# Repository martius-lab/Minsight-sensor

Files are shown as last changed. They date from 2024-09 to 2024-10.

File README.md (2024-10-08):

# Minsight: A Fingertip-Sized Vision-Based Tactile Sensor for Robotic Manipulation

This project provides manufacturing details and files for [Minsight](https://onlinelibrary.wiley.com/doi/full/10.1002/aisy.202300042). It is a soft fingertip-sized tactile sensor that can sense 3D forces over its whole sensing surface.

The corresponding paper is titled "[Minsight: A Fingertip-Sized Vision-Based Tactile Sensor for Robotic Manipulation](https://onlinelibrary.wiley.com/doi/full/10.1002/aisy.202300042)", published in *Advanced Intelligent Systems*, 2023. 

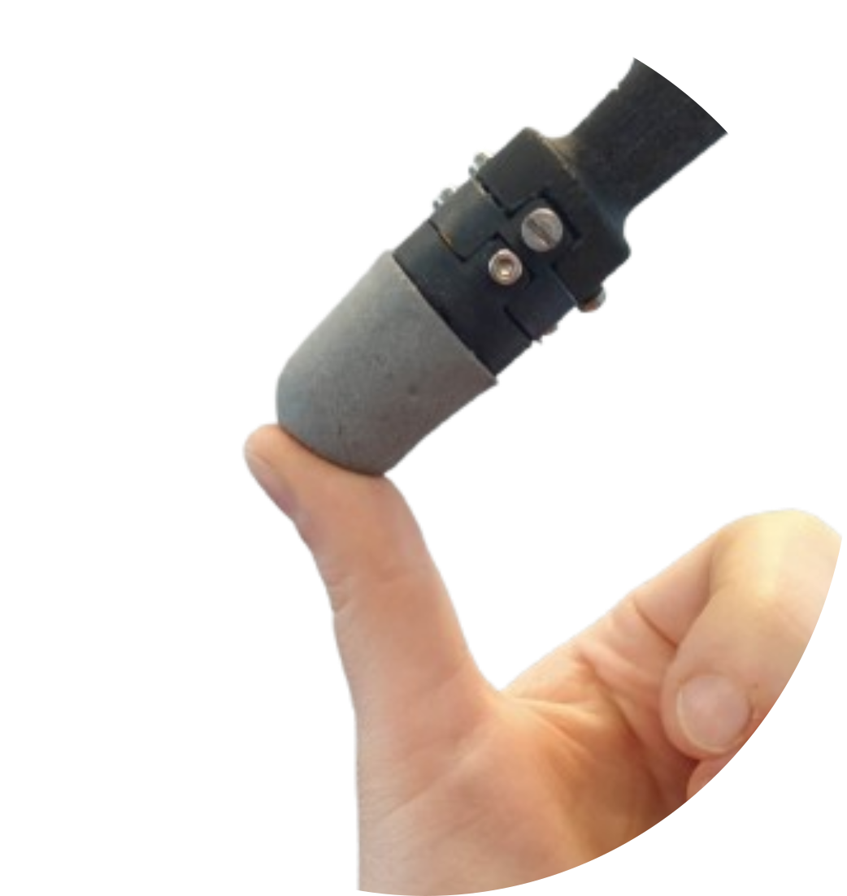
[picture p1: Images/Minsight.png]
<p align="center">
  
This work was done by Iris Andrussow, Huanbo Sun, Katherine J. Kuchenbecker, Georg Martius at the Max Planck Institute for Intelligent Systems. Please find the citation information at the end of the README
  
# Abstract
Intelligent interaction with the physical world requires perceptual abilities beyond vision and hearing; vibrant tactile sensing is essential for autonomous robots to dexterously manipulate unfamiliar objects or safely contact humans. Therefore, robotic manipulators need high-resolution touch sensors that are compact, robust, inexpensive, and efficient. The soft vision-based haptic sensor presented herein is a miniaturized and optimized version of the previously published sensor Insight. Minsight has the size and shape of a human fingertip and uses machine learning methods to output high-resolution maps of 3D contact force vectors at 60 Hz. Experiments confirm its excellent sensing performance, with a mean absolute force error of 0.07 N and contact location error of 0.6 mm across its surface area. Minsight's utility is shown in two robotic tasks on a 3-DoF manipulator. First, closed-loop force control enables the robot to track the movements of a human finger based only on tactile data. Second, the informative value of the sensor output is shown by detecting whether a hard lump is embedded within a soft elastomer with an accuracy of 98\%. These findings indicate that Minsight can give robots the detailed fingertip touch sensing needed for dexterous manipulation and physical human–robot interaction.

# Working Mechanism

Minsight is a vision-based tactile sensor. Is uses a camera as the transducer and can detect small deformations of an elastic shell from the inside. To create 3D forces, we use the photometric stereo effect to learn an end-to-end mapping of camera image to a force map over the full sensor surface. 

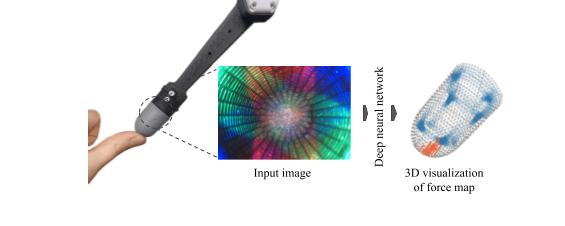
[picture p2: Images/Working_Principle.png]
<p align="center">

# Mechanical Components

Like [Insight](https://github.com/Huanbo-Sun/Haptics-for-Robots-Insight/blob/master/README.md), Minsight uses a hybrid structure of a soft elastomer shell enclosing a stiff metal skeleton to ensure high sensitivity and robustness. The soft elastomer deforms easily and can detect contact with high sensitivity. The metal skeleton provides a stiff global shape and helps to sustain high-impact forces.

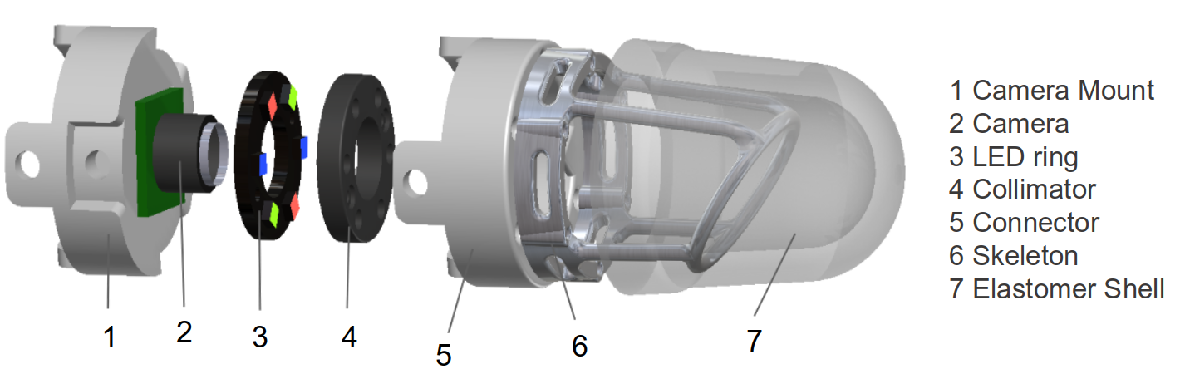
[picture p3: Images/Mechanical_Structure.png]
<p align="center">

## Soft Elastomer Shell
- 3D Printer: [Formlabs Form 3](https://formlabs.com/eu/3d-printers/form-3/)
- 3D Printing Material: [Tough Resin FLTOTL05](https://formlabs.com/store/tough-2000-resin/). *Note: The original material is not available anymore, but an updated version.*
- Mold Design: 
  - [Mold](CAD/Mold/)
- Elastomer Material:
  - [EcoFlex 00-30](https://www.smooth-on.com/products/ecoflex-00-30/)
  - [Aluminum Powder 65 Micrometer, 99% Pure](https://www.amazon.de/Aluminumpulver-Aluminium-Pulver-Alupulver-Zus%C3%A4tze/dp/B06WRTGP2Y)
  - [Aluminum Flake 75 Micrometer](https://www.metallpulver24.de/de/aluminiumpulver-flaky-silber.html)
       
## Rigid Metal Skeleton
- 3D Printer: [ExOne X1 25 Pro](https://www.exone.com/en-US/Resources/News/X1-25PRO)
- 3D Printing Material: [AlSi10Mg-0403 Alluminum Alloy](https://www.shapeways.com/materials/aluminum)
- Geometry Design: [Skeleton](CAD/skeleton.STEP)
- Printing Service: [Shapeways](https://www.shapeways.com/)
       
## Camera Holder and Sensor Base
- 3D Printer: [Formlabs Form 3](https://formlabs.com/eu/3d-printers/form-3/)
- Material: [Standard Black](https://formlabs.com/de/shop/black-resin/)
- Design: [Holder](CAD/camera_holder.STEP), 
          [Base](CAD/sensor_base.STEP)
      
# Imaging System

### Camera

- [ MISUMI YD-B31111LH-158A-03 with Connector and USB 3.0](https://www.misumi.com.tw/en/about/aboutus)

### LED Ring
- LEDS: [Würth Elektronik SMD LEDs 150044M155220](https://www.mouser.de/ProductDetail/Wurth-Elektronik/150044M155220?qs=rQFj71Wb1eUvmcUtzGYYDA%3D%3D)
- PCB Design: [PCB/led_layout]
- Example Supplier: [Beta Layout](https://de.beta-layout.com/leiterplatten/)
     
### Collimator
- 3D Printer: [Formlabs Form 3](https://formlabs.com/eu/3d-printers/form-3/)
- Material: [Standard Black](https://formlabs.com/de/shop/black-resin/)
- Geometry Design: [Collimator](CAD/collimator.STEP)

# Manufacturing and Assembly Instructions

More detailed instructions for manufacturing and assembly are provided [here](Instructions/Manufacturing_Instructions.pdf)

## Required equipment for manufacturing and assembly: 
- Vaccum Chamber (5 Pa)
- Scale with 0.1 g resolution
- Screwdriver
- Mold release / Inhibit-X
- 6 x M1.4x6 screws
- 6 x M2.5x4 screws
- 6 x M2 nut
- Gloves, safety goggles and mask
- Mixing container and spatula

# Calibration
We use a custom test bed to calibrate the sensor in a controlled way, collecting both normal and shear forces.
For the technical details of this test bed, please refer to the [Testbed section](https://github.com/Huanbo-Sun/Haptics-for-Robots-Insight/blob/master/README.md#testbed) in the Insight Documentation 

# Software

Data processing for the raw data collected during calibration can be found in a [jupyter notebook](Code/minsight_training/data_processing/dataset_preprocessing.ipynb). \
We furthermore provide code for training the force mapping on the preprocessed data [here](Code/minsight_training/training/). \

We also provide ROS nodes to run Minsight's force map inference and visualization [here](Code/). The provided config files are examples, valid only for an exisiting demo sensor and should to be replaced with the respective calibration files for any new sensor. 

## Reproducing results in the Minsight paper

To reproduce error plots and inference times, refer to the respective scripts in the [Code section](Code/minsight_training/).\
To reproduce results for the lump classification experiment, use [this code](Code/lump_classification/), together with the data published in https://doi.org/10.17617/3.AEDHD1.

# Citation
Please use the following citation if you make use of our work:
## BibTex
``` citation
@article{https://doi.org/10.1002/aisy.202300042,
author = {Andrussow, Iris and Sun, Huanbo and Kuchenbecker, Katherine J. and Martius, Georg},
title = {Minsight: A Fingertip-Sized Vision-Based Tactile Sensor for Robotic Manipulation},
journal = {Advanced Intelligent Systems},
volume = {5},
number = {8},
pages = {2300042},
doi = {https://doi.org/10.1002/aisy.202300042},
url = {https://onlinelibrary.wiley.com/doi/abs/10.1002/aisy.202300042},
year = {2023}
}
```
### RIS
``` citation
TY  - JOUR
T1  - Minsight: A Fingertip-Sized Vision-Based Tactile Sensor for Robotic Manipulation
AU  - Andrussow, Iris
AU  - Sun, Huanbo
AU  - Kuchenbecker, Katherine J.
AU  - Martius, Georg
PY  - 2023
DO  - https://doi.org/10.1002/aisy.202300042
JO  - Advanced Intelligent Systems
JA  - Adv. Intell. Syst.
SP  - 2300042
VL  - 5
IS  - 8
PB  - John Wiley & Sons, Ltd
SN  - 2640-4567
UR  - https://doi.org/10.1002/aisy.202300042
Y2  - 2024/09/16
```

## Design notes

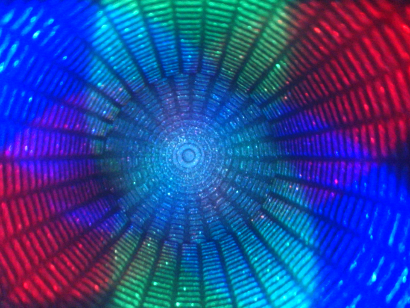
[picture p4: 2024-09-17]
Code/minsight_runner_ros/default_2.png

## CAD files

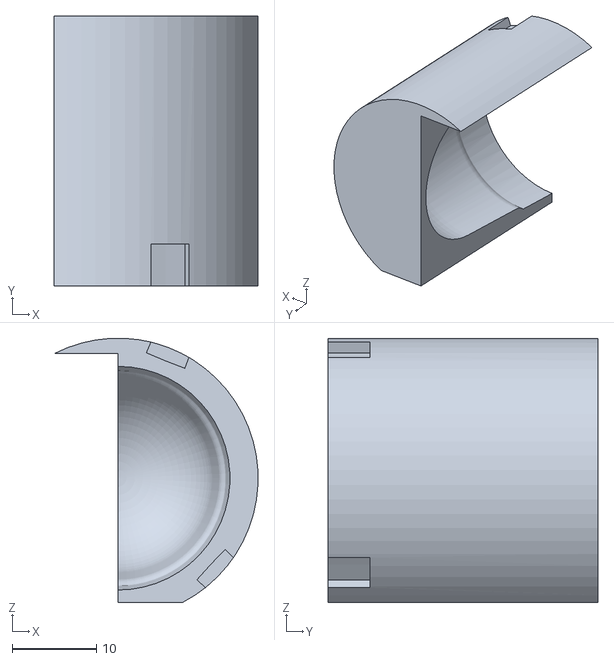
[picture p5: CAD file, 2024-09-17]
CAD/Mold/Mold_1.STL
24.2 x 32.0 x 31.3

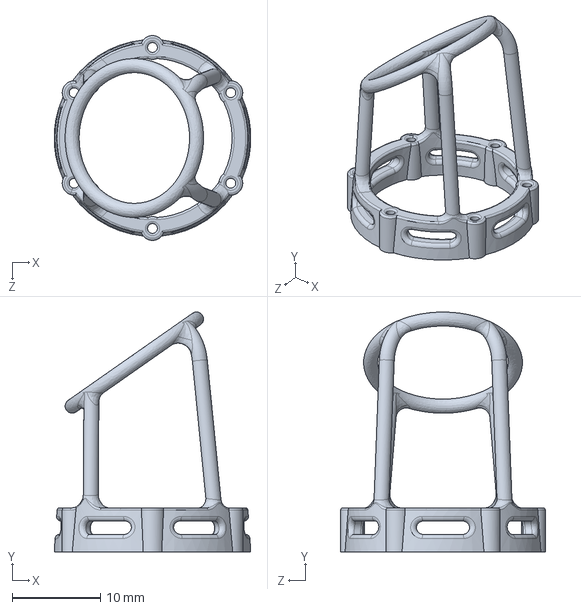
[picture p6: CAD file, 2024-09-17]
CAD/skeleton.STEP
22.3 x 27.2 x 23.2 mm

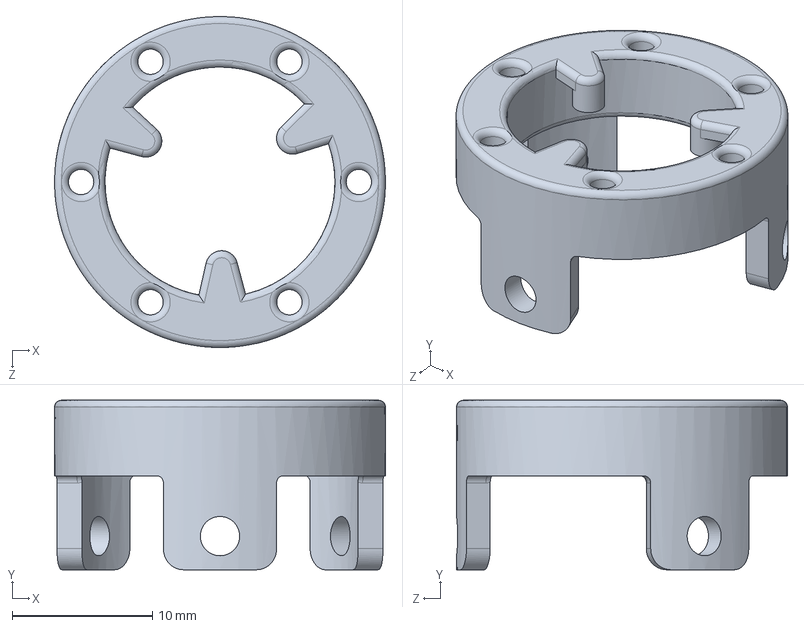
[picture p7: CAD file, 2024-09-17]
CAD/camera_holder.STEP
23.6 x 12.1 x 23.6 mm

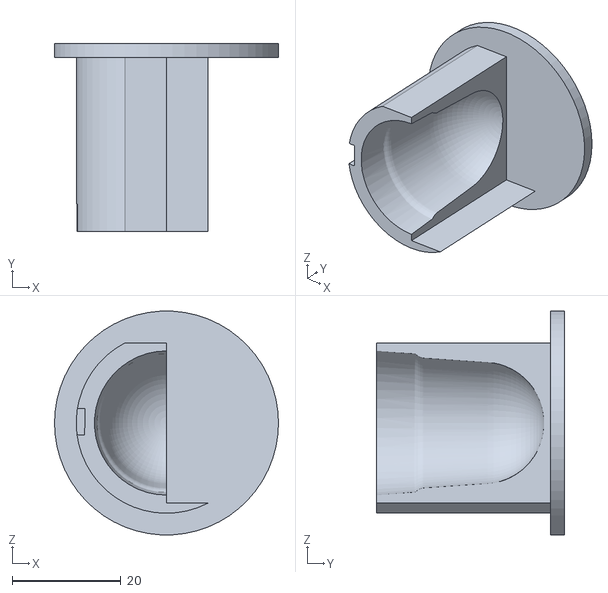
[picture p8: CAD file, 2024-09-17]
CAD/Mold/Mold_2.STL
41.2 x 34.5 x 41.1

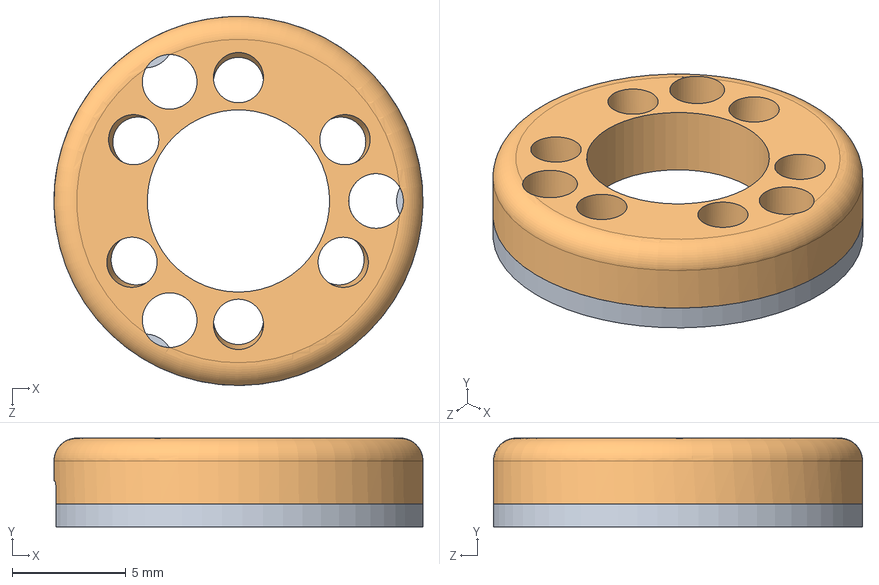
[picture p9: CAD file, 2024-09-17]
CAD/collimator.STEP
16.2 x 3.90 x 16.2 mm

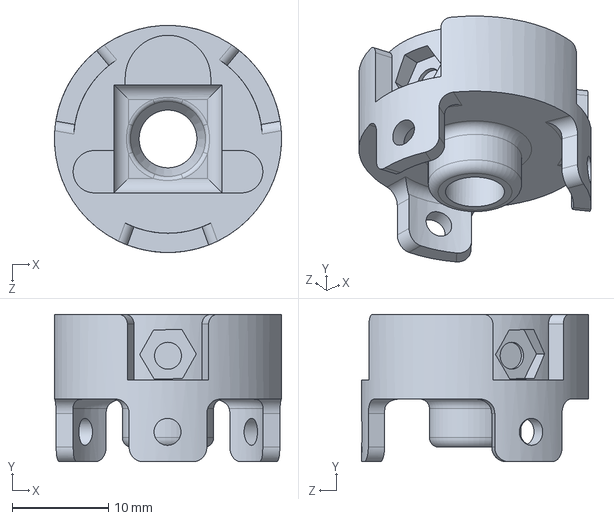
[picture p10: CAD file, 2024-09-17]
CAD/sensor_base.STEP
23.6 x 15.3 x 23.6 mm

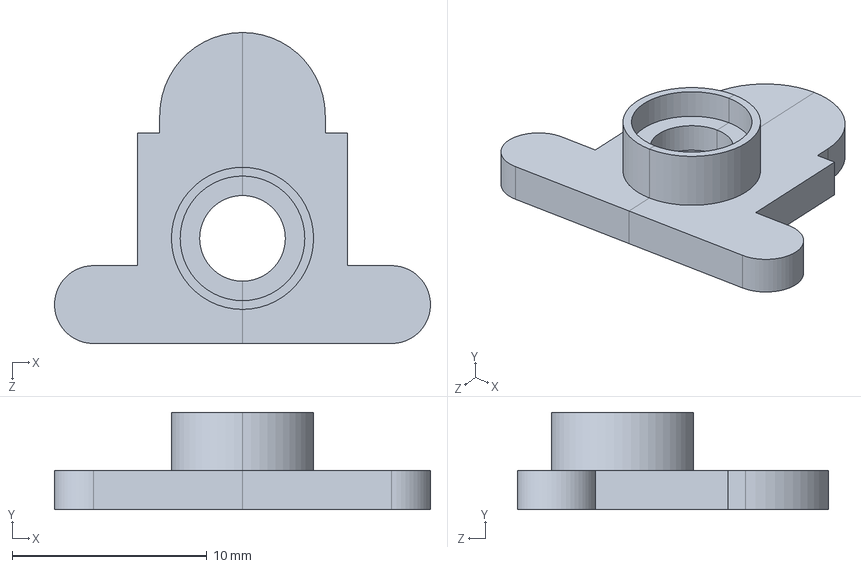
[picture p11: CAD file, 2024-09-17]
CAD/cover_plate_camera_holder.STEP
19.3 x 5.00 x 16.0 mm

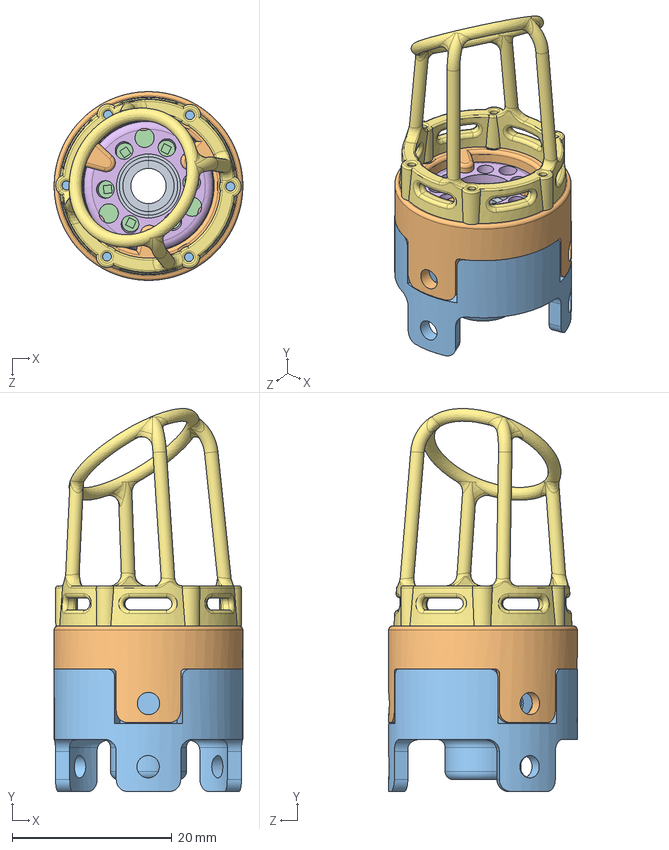
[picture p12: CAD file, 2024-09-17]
CAD/sensor_mount.STEP
23.6 x 47.9 x 23.6 mm
cover_plate_camera_holder
camera_holder
sensor_base
custom_LED_ring
collimator
Skeleton_rigid_struct_with_hinge

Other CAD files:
CAD/camera_holder.STL
CAD/collimator.STL
CAD/cover_plate_camera_holder.STL
CAD/sensor_base.STL
CAD/skeleton.STL

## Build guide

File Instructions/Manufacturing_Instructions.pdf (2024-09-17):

Instructions for manufacturing the Minsight Sensor-Shell

1. Preparation of the mold:
a. Connect the two halves of the outer mold tightly, but using two elastic rings. When coming fresh out of the printer, use a product like Inhibit-X to prevent problems with curing.
b. Screw the skeleton on the insert part of the mold in the following orientation:

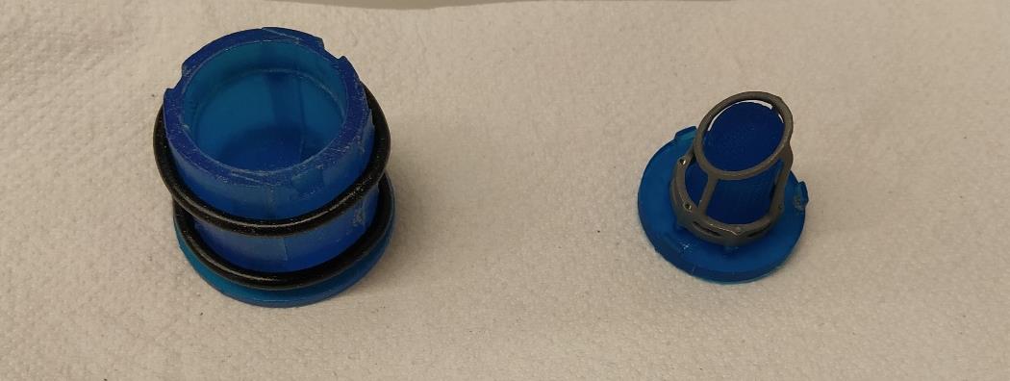
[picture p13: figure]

Do not over tighten the screws and make sure that the skeleton is centered.
c. Grease the outer mold with a thin layer of mold release. Do not put mold release on the insert, as it changes the reflective properties of the Minsight shell!
2. Production of the silicone mixture:
a. Prepare a plastic vessel and a wooden spatula to stir the elastomer components.
b. Shake the two different silicones well and stir them.
c. Fill 15g Smooth-On EcoFlex part A into the vessel.

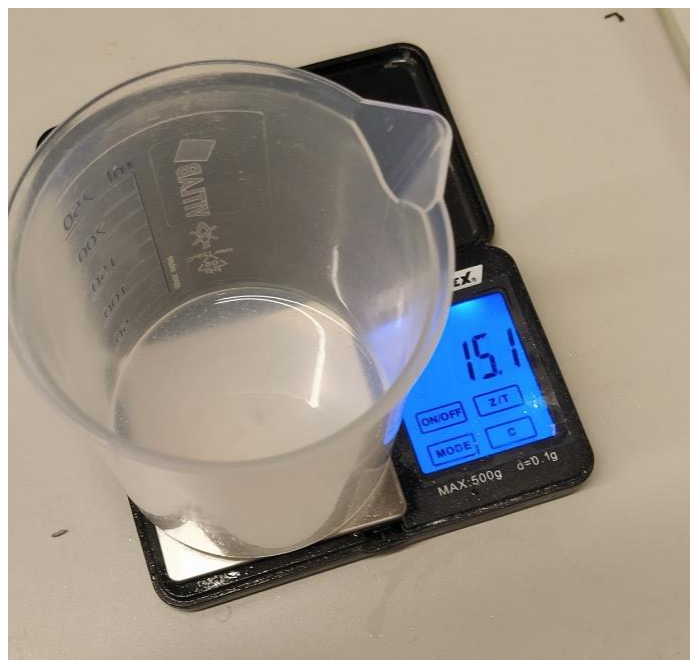
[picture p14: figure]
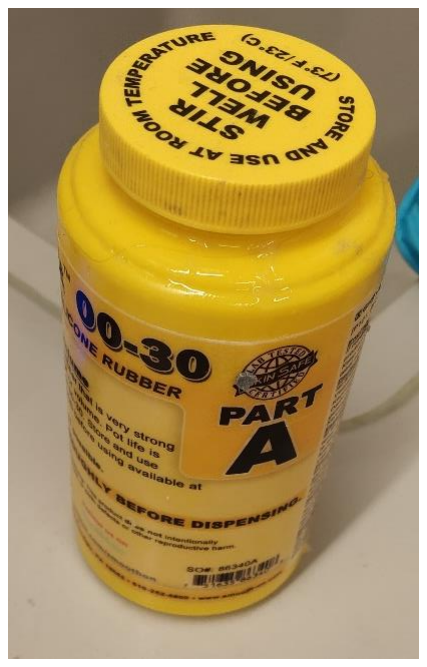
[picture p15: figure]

d. Put on a mask and safety glasses before proceeding. Now add 3g of aluminium powder as well as 0.1 g aluminium flakes with a teaspoon and stir it well with the wooden spatula.

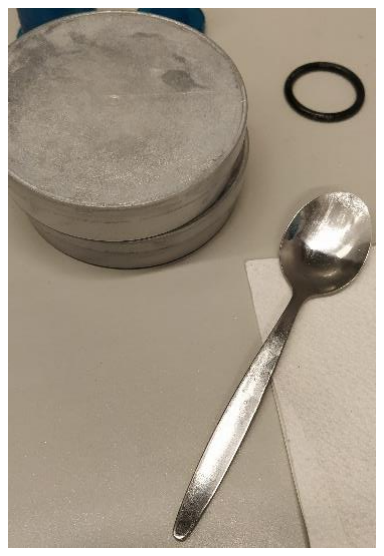
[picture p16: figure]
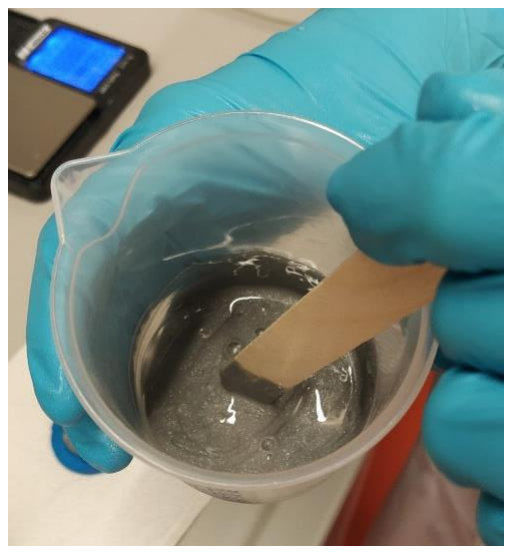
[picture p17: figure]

e. Then add 15g Smooth-On EcoFlex part B and stir again.
f. To ensure homogeneity of the material, degas the silicone mixture for 5 minutes at 5 Pa. Afterwards, make sure to open the valve slowly and release the pressure.
3. Fill the mixture carefully (like pouring a beer) into the mold and degas again for 5 minutes.

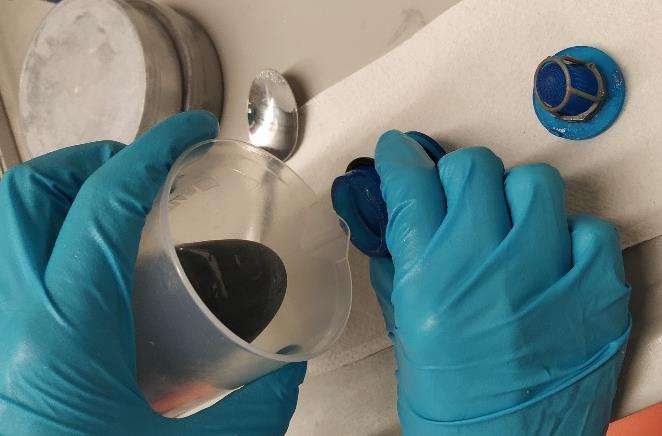
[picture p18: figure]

4. Now carefully place the upper part of the mold with the skeleton onto the lower part filled with the silicone mixture. Make sure that the two parts of the mold fit together correctly but do not press too much on it.
5. Let the whole shell cure for a minimum of 4 hours.
6. After curing, use a spatula to open the mold and unscrew the skeleton. Disconnecting the molded shell from the insert is tricky, Therefore insert the a thin spatula between the silicone and the mold, and lever the sensor shell upwards so that air can enter. Repeat this in several places to release the shell from the mold. The edge of the shell can then be trimmed with scissors.

3D printing the the base of the sensor

Use an SLA 3D printing method available to you for the sensor base, camera holder and collimator. Before curing the parts, insert nuts into the cutouts in the sensor base.

Assembling the sensor

Screw the skeleton and shell combination to sensor base and

insert the collimator in the correct orientation.

Remove the built-in white LED ring on top of the camera lens, but keep the thin power cables intact. They will later power the custom LED ring.

Open the connector of the camera USB cable and thread it through the
camera holder. The camera should have a certain
orientation to optimize the viewing angle (see picture).
Then place the two small camera holder parts around the lens
of the camera and insert it into the camera holder.
Carefully close the camera cable connector again.

Now place the LED ring on the collimator in the correct orientation and solder the power cables to the camera power supply. Screw the lower and upper parts of the mount together with the three screws.

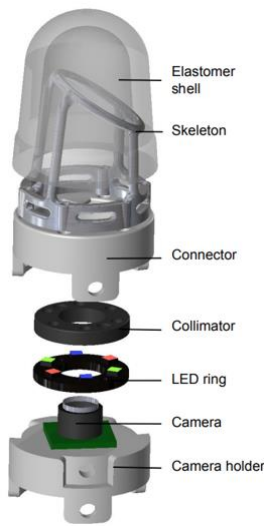
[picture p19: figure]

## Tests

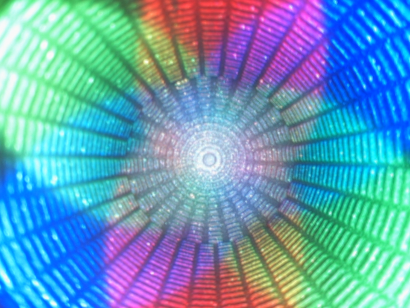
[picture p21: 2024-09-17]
Code/minsight_runner_ros/config/calibration_files/C1/NoContact_avg.png

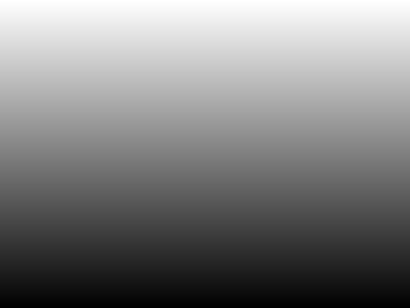
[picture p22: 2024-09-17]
Code/minsight_runner_ros/config/calibration_files/C1/gradient2.png

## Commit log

2024-09-17 Update design files and instructions
    [Mold_1.STL, Mold_2.STL, camera_holder.STEP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]
2024-09-17 Add comment about PCB
2024-10-08 Add PCB files
